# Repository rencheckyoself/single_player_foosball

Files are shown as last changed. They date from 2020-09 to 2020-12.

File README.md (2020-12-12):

# Single Player Foosball Table

[Video](https://mrencheck.wixsite.com/michaelrencheck/single-player-foosball)

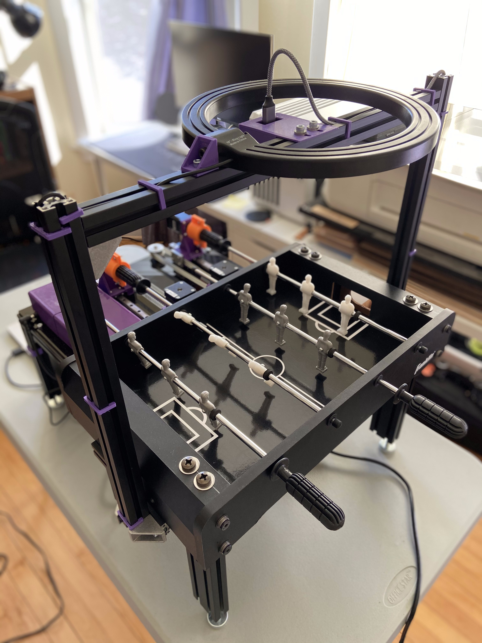
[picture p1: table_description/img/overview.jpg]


## Dependencies
The following are other software packages required to run the software for the table:
  - ROS Melodic
  - Pololu tic Software
  - OpenCV

## Installation

Begin by installing some of the external software dependancies:
  - The instructions for installing ROS Melodic are found [here](http://wiki.ros.org/melodic/Installation/Ubuntu).

  - The instructions to install the Pololu tic Software are found [here](https://github.com/pololu/pololu-tic-software). See relevant section in the BUILDING.md file to build the library from source, these were the [directions](https://github.com/pololu/pololu-tic-software/blob/master/BUILDING.md#building-from-source-on-linux-for-linux) I used.

After installing these create a new catkin workspace and clone this repository:

```
mkdir SinglePlayerFoosball
cd SinglePlayerFoosball
git clone https://github.com/rencheckyoself/single_player_foosball.git src
```

Then go into the repository and use wstool. This will download my forked version of the oCam package. It has been updated to function properly with ROS Melodic and adds some extra configuration for including the main launch file.
```
cd src
wstool update
```

Finally, go back to the top level of the directory and build the workspace:
```
cd ..
catkin_make
```

## Table Assembly

The CAD and Bill of Materials are located at this google drive [link](https://drive.google.com/drive/folders/1ccFXVZE29upyrK4uFZC98GBmM7wjYVV8?usp=sharing). You will an assembly procedure along with pictures depicting some of my build process and final assembly.

## Visualizations

This workspace includes two methods of visualizations, a urdf model displayed in rviz and an OpenCV window of the camera feed with added data.

#### rviz
 The urdf model will responds to all of the joint state messages displaying the positions that the gameplay node has decided to move to. It will also show a marker for most recent location of the ball.

#### OpenCV window
This window is generated by the `opencv_viewer` node. This will update everytime the camera sends a new image. The top corner shows the approximate frame rate of the images coming in. A red dot at the location of the most current ball position at the time an image is received. If the `ball_tracking` node does not detect a ball, the dot will appear in the upper left hand corner of the image. Also displayed is the player angle detection results. A white rectangle will show the ROI the `player_tracking` node is using and when the rods move, another rectangle will bound the detected player. A blue rectangle means the player is detected as down and the ball cannot pass underneath, green means the players are raised and at the end of a kick, red means the players are raises with their feet closest to the goal.

## Required Configuration
1. Update `table_motor_control/config/motor_ids.yaml` with the serial numbers for your specific TIC boards and update motor settings.

2. Calibrate your camera. I have included the calibration file for my camera in the ocam package files, but it may not be suitable for yours.
3. If you are using a different ball and/or table you may need to retrain the cascade classifier.
4. Update the pixel locations for the known pairs of world locations to pixel locations in order to calculate the homography.
5. Update the parameters to generate the joint_states/stepper commands to account for the differences in the camera position and calibration.
6. Update the parameters for the player angle detection.

### Tic Serial Numbers and Settings:
Once everything is wired and after installing the tic software, open a terminal and use the command `ticgui`. Plug in boards one at a time and copy over the serial number to the `motor_ids.yaml` file. Be sure that the serial numbers are copied over to the correct parameter in the yaml file.

Then you will want to determine the appropriate settings, namely the motor direction, max velocity, max acceleration, and current limit. The easiest way to do this is using the ticgui. Use [this](https://www.youtube.com/watch?v=-cAjdT6QN_w) quickstart video walkthrough for how to set the values. Then

### Camera Calibration:
There is a calibration file included in the ocam package from the .rosinstall file. This may or may not work for your ocam camera, so in order to generate your own calibration file, use the [`camera_calibration`](http://wiki.ros.org/camera_calibration) package in the ROS Image Pipeline. There is an included checkerboard in the `table_vision_sensing/calibration` directory to print out and use for the calibration.
Use the commands below to start the calibration using the included checkerboard:
```
roslaunch ocam ocam_ros.launch show_image:=false

rosrun camera_calibration cameracalibrator.py --size 7x5 --square 0.033 image:=/camera/image camera:=/camera
```
Once everything launches, move the checkerboard around in the image until the calibration button becomes available. Click calibrate and wait for the process to finish. The location of the output with be show in the terminal. Copy the `camera.yaml` generated by the calibration into `ocam/config`.

### Training the cascade classifier:
I have included the model I trained in the `cascade_data` folder, but if you don't have the same table/ball as my set up or want to experiment you can train your own cascade model.

OpenCV provides a great [walk-through](https://docs.opencv.org/3.4/dc/d88/tutorial_traincascade.html) for how to use their provided tools to generate the final output. Read through this first, then use the following to help with collecting your image dataset and generating the trained model.

To collect your own image set using the camera mounted over the table use the `capture_training_image.launch` file. This file will start nodes that create a new directory inside the `table_vision_sensing` package called `training_data`. Inside will be the `.dat` files required for the OpenCV training pipeline and two directories corresponding to the saved images. After launching, two windows will be displayed one called "Capture for background" and "Capture for ball".
 - To save an image for the background/negative set, click on the "Capture for background" window and click the "s" key. The picture will be saved in `training_data/background` directory and the proper annotation recorded in the `background.dat` file. All of the images in the background set should not contain the ball.
 - To save an image for the ball/positive set, click on the "Capture for ball" window and click the "s" key. The picture will be saved in the `training_data/ball` directory. Use the opencv tool for annotating positive images after all have been collected.

If you want to add you your collected set later, just relaunch the file and the numbering for the ball and background images will pick up where each set left off. Modify the `image_group` launch file argument to save positive images to a new directory.

```
roslaunch table_vision_sensing capture_training_data.launch image_group:=ball
```

You can also use the camera to capture gameplay footage and then use vlc to extract frames from the video and save them as images. I used the camera launch file then used a screen recorder to capture the OpenCV window.

```
roslaunch table_vision_sensing start_ocam.launch view_image:=true show_ball_pos:=false show_player_angle:=false
```

Once the video is captured, either follow [this](https://www.raymond.cc/blog/extract-video-frames-to-images-using-vlc-media-player/) to use the vlc gui to save out frames as images or use the following command:
```
cd [path_to_workspace]/src/table_vision_sensing
mkdir training_data/gameplay_frames
cvlc [video_name] --video-filter=scene --vout dummy --scene-ratio 60 --scene-path src/table_vision_sensing/training_data/ball/ --scene-prefix gameplay --start-time 0 --stop-time 120 vlc://quit
```
- --scene-prefix: a unique name to append to the beginning of each saved frame. (optional)
- --start-time: time to start at in seconds (optional)
- --stop-time: time to stop at in seconds (optional)
- --scene-ratio: how often to save frames. i.e. a scene-ratio of 60 for a video recorded at 60 fps will save 1 image every second.

Each time you run the command the number will always start at 1 regardless of the time span used so if your want to use a bunch of small pieces of the video, modify the --scene-prefix to avoid overwriting previously generated images. Also if you use the command line, I got a lot of error messages that popped up, but it didn't effect the functionality. The command will terminate once all of the frames have been saved. See the [VLC Documentation](https://wiki.videolan.org/VLC_command-line_help) for more information or use `vlc --full-help`.

Data collection tips:
- Collect all of the pictures with the overhead light on.
- If your ball has a pattern, be sure to rotate the ball between still image shots.
- Take picture of the ball partially occluded by the players and rods.
- Take background pictures with the players in various orientations.
- Take pictures of the ball when it is moving fast as well as slow.

You will want to collect 2:1 positive to background images. I used roughly 1000 positive images and 500 background images. After all of your images are collected, use the integrated annotation tool provided by OpenCV to properly annotate the ball/positive image set. It should take about 45min to annotate 1000 positive images. Using the following:
```
cd [path_to_workspace]/src/table_vision_sensing/training_data
opencv_annotation --annotations  -ball.dat --images ball/
```

After the annotations have been completed, use the provided OpenCV tool to create the positive image set .vec file. Use the following command:
```
cd [path_to_workspace]/src/table_vision_sensing/training_data
opencv_createsamples -vec ball.vec -info ball.dat -w 24 -h 24 -num [number of images]
```

After the .vec file has been generated, use the cascade trainer to get the trained cascade model for ball detection. The following was my configuration but your mileage may vary. I also tweaked the minHitRate to 0.999 and maxFalseAlarmRate to 0.1 as well. See the OpenCV documentation for all of the possible training parameters to play with.
```
cd [path_to_workspace]/src/table_vision_sensing/training_data
mkdir ../cascade_data
opencv_traincascade -data ../cascade_data/ -vec ball.vec -bg background.dat -w 24 -h 24 -numPos 700 -numNeg 500 -numStages 25
```

### Homography Calculation
In order to transform the ball's image coordinates to world coordinates, the system needs to know some known pairs. So you will need to update the `homography_config.yaml` file in the `table_gameplay_ai/config` directory to adjust for the slight differences in the camera location. Included in that directory is a template corresponding to the world positions already listed in the `homography_config.yaml` file and an .stl for a stand that neatly fits into the circles on the template. Print out two copies of the template, attach them along the middle and and place it on the field.

Then start up the ball tracking node, echo the `/BallPosition` topic in a separate terminal and record the average `(x,y)` pixel values in the `.yaml` file. Be sure that as the image coordinates are entered in to the .yaml file, they are entered on the correct line.

```
roslaunch table_vision_sensing start_tracking.launch view_image:=true
rostopic echo /BallPosition
```

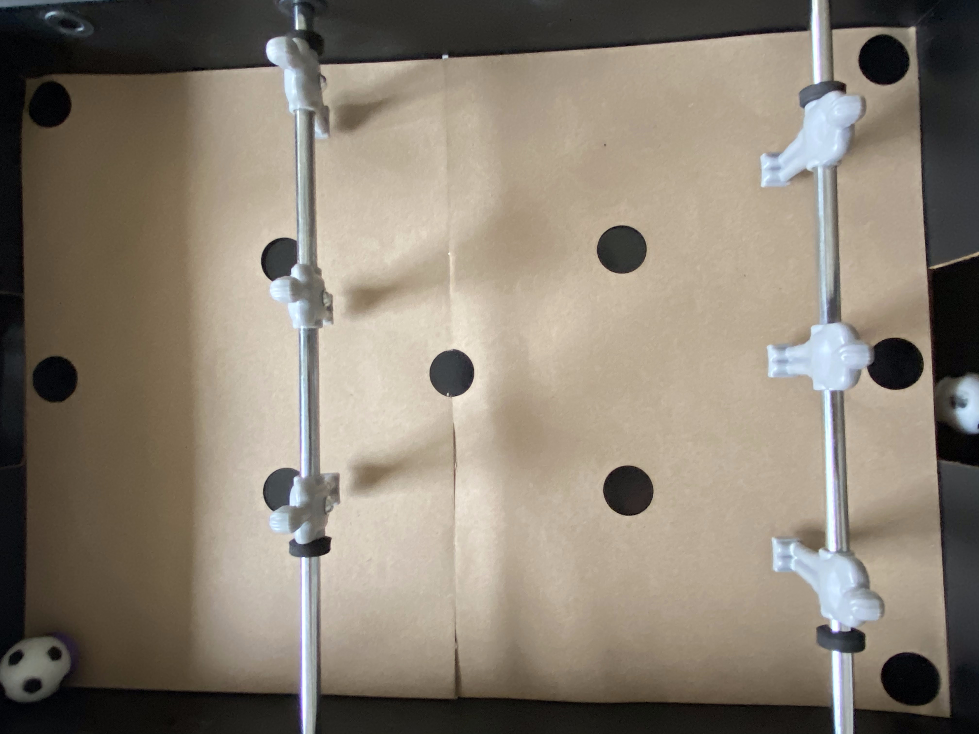
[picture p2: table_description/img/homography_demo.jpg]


### Command Generation Configuration

The two parameters that will most likely need adjusted are the `def_rod_xpos` and the `fwd_rod_xpos` in the `command_generation_config.yaml`. These parameters define the x position of the ideal location to strike the ball for each rod. In order to update these, use `start_game.launch` but leave the motors unpowered so the rods stay stationary. Position the players vertically and place the ball directly in front of a player. Either use rviz or echo the `visualization_marker` topic to see the x position of the ball in the world coordinates. Record this value in the `command_generation_config.yaml` file for the automated defensive rod and the automated offensive rod.

If you are using a different sized table, you will need to update the joint limits as well to account for linear travel of the rod. You may also want to update `table_params.yaml` in the `table_description` package in order to correct the visualization. For example, the rods on my table can travel 0.09m linearly. The urdf assumes the 0 position is in the middle so the joint limits will be at -0.45 and 0.45. For my table, 0.09m corresponds to roughly 240 steps to make the rod travel the full distance. When the game starts up, the gameplay node assumes the rod is already in 0 position. I chose to have the lower stepper position limit be the 0 position which makes the upper stepper position limit 240.

You can also modify the `linear_hysteresis` parameter to make the linear motion more or less sensitive to changes in the ball position.

### Player Angle Detection Configuration

You may need to adjust the player angle detection parameters in `player_angle_detection.yaml` to account for your camera's position and calibration. Use the `start_tracking.launch` file with `view_image:=true` to display results of the player angle detection. First modify the roi_x and roi_y, roi_width, and roi_height so that the large white rectangles capture one of the players on the two automated rods.

After the windows are properly aligned use rostopic echo to listen to the `\Def_RodState` and `\Fwd_RodState`. The player detection works using background subtraction, so in order use the detection the rod needs to move. Rotate the rod parallel to the table (like it just finished a kick) and slowly move it back and forth. Update `end_kick_x` value to a something a few less than the `min_x_value` shown on the topic and update `end_kick_width` to something a few less than the maximum `bounding_rect_img.width` value shown on the   topic.

If the bounding rectangle is not showing up when the player is moving, decrease `area_limit`. If small contours that are not part of the player are being detected, increase `area_limit`.

## How to Run:

Position players in the assumed starting position: the players feet down, perpendicular to the table with the rod against the wall closest to the motors, like so:

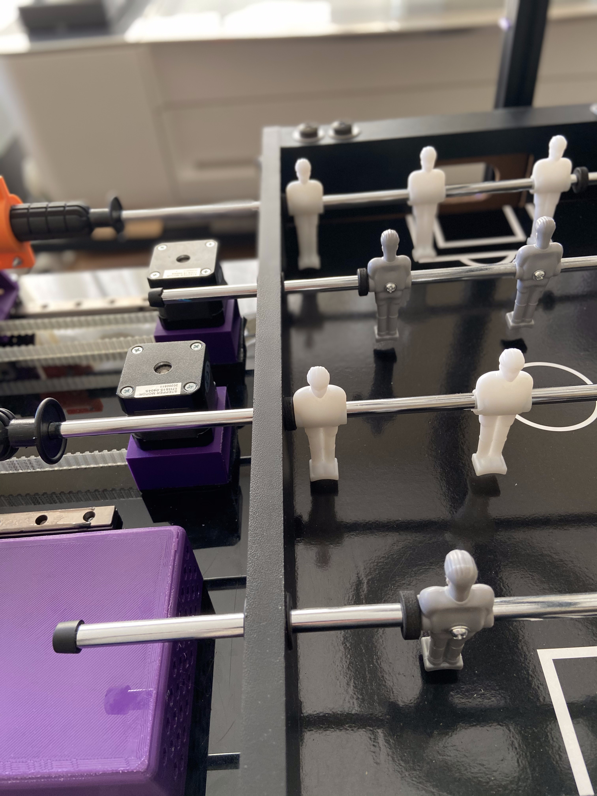
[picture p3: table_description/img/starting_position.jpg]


Plug in power supply to the barrel jack connector, then plug it into the wall and flip the switch to turn on the table.

Launch main launch file:
```
roslaunch table_gameplay_ai start_game.launch with_rviz:=false view_image:=false
```

Throw ball onto table and play!

Change the `mode` argument type to change the play style of the table:
- 0: (default) Open loop. Relies on the accuracy of the stepper controller position count to move.
- 1: Infinite spin. The linear position control stays the same as mode 0, but the rods will continually spin.
- 2: Rotation feedback. Same linear control scheme, but the angular control uses the player angle detection to account for any slipping during gameplay.

## Packages

### Description
This package provides a urdf model of the foosball table that can be displayed in rviz.

Launch Files:
- `view_table.launch`: Launch rviz and display the urdf along with the joint state publisher gui.
  - use_gui, default: true. Set this to false to turn off the joint state publisher
  - rviz_config, the location of the rviz configuration file
  - with_rviz, default: true. Set to false to not launch rviz.

Configuration:
- `table_params.yaml`: measurements of the physical table. Changing these will update the urdf.

### Control
This package provides an interface to work with the TIC Stepper Controller API through ROS by offering services.

Launch Files:
- `tic_controllers.launch`: launch all of the nodes to interact with the motors

Nodes:
- `tic_cmd`: node that starts up services to manually interact with each controller. If a controller is not connected, this will not launch properly.

Configuration:
- `motor_ids.yaml`: contains all of the identifying information for each controller. This file must be updated with the serial numbers for your purchased boards.
- `*_settings.txt`: these files contain the detailed settings for each of the motors. They were initially generated by exporting the settings using the ticgui. These files can be used to update the settings of a given tic while everything is running using the `*_update_settings` service. The can also be uploaded using the ticgui tool.

### Vision
This package is currently set up to follow the [ROS image_pipeline](http://wiki.ros.org/image_pipeline) structure. The `table_vision_sensing` package is set up to be camera agnostic, so feel free to use your own camera in place of the one linked in the parts list. You will need to modify the launch files to use your own camera.

Launch Files:
- `start_ocam.launch`: Launch the camera and view the rectified image
  - view_image, default: false. Set this to false to the rectified image.
  - show_ball_pos, default: true. Set this to false to not display a red dot for the ball position on the image feed.
  - show_player_angle, default: true. Set to false to not display bounding rectangles for the player angle.
- `start_tracking.launch`: Launch the ball and player tracking nodes. set view_image to true to view the output.
  - view_image, default: false. Set this to false to the rectified image.
- `capture_training_data.launch`: Launch everything to collect images to train the cascade classifier
  - image_group, default: "ball". A string to use as the name for a directory of positive images.

Nodes:
 - `ball_tracking`: Use the trained cascade model to find and publish the ball's pixel location
 - `opencv_viewer`: Listen to an image topic and display the image along with the ball position and player angle info
 - `player_tracking`: Use background subtraction and contour fitting to determine the approximate angle of the player
 - `training_image_capture`: Listen to an image topic to collect data to train a cascade classifier

Configuration:
 - `player_angle_detection.yaml`: contains all of parameters to define the window to analyze and the parameters to detect if the players are raised and which side the feet are closest to.

### Gamplay
This package is used as the main decision making pipeline based on the detected ball position and creates a joint state message that can be used by the urdf model for testing or converted to stepper commands using the `table_motor_control` package.

Launch Files:
- `start_game.launch`: Launches everything to play a game of foosball against the table
  - with_rviz, default: true. Set to false to not launch rviz.
  - view_image, default: false. Set this to false to the rectified image.
- `start_simulation.launch`: Uses the real ball position on the table, but does not actuate the real motors only the urdf model in rviz.

Nodes:
- `follow_ball`: The main node to decide the action and publish the joint state message.

Config:
- `homography_config.yaml`: contains know pairs of world location to pixel location in order to calculate the homography.

## Resources
- [Tic User Manual](https://www.pololu.com/docs/0J71)
- [OpenCV Documentation](https://www.docs.opencv.org/master/)
- [ROS Image Pipeline](http://wiki.ros.org/image_pipeline)
- [oCam Manual](http://withrobot.com/en/camera/ocam-1cgn-u-t/)

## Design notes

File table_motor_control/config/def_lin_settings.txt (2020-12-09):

# Pololu Tic USB Stepper Controller settings file.
# https://www.pololu.com/docs/0J71
product: T825
control_mode: serial
never_sleep: false
disable_safe_start: false
ignore_err_line_high: false
auto_clear_driver_error: true
soft_error_response: decel_to_hold
soft_error_position: 0
serial_baud_rate: 9600
serial_device_number: 14
serial_alt_device_number: 0
serial_enable_alt_device_number: false
serial_14bit_device_number: false
command_timeout: 0
serial_crc_for_commands: false
serial_crc_for_responses: false
serial_7bit_responses: false
serial_response_delay: 0
vin_calibration: 0
input_averaging_enabled: true
input_hysteresis: 0
input_scaling_degree: linear
input_invert: false
input_min: 0
input_neutral_min: 2015
input_neutral_max: 2080
input_max: 4095
output_min: 0
output_max: 240
encoder_prescaler: 1
encoder_postscaler: 1
encoder_unlimited: false
scl_config: default
sda_config: default
tx_config: default
rx_config: default
rc_config: default
invert_motor_direction: false
max_speed: 13000000
starting_speed: 0
max_accel: 1300000
max_decel: 0
step_mode: 1
current_limit: 384
current_limit_during_error: -1
decay_mode: slow
auto_homing: false
auto_homing_forward: false
homing_speed_towards: 1000000
homing_speed_away: 500000

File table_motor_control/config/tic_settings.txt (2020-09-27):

# Pololu Tic USB Stepper Controller settings file.
# https://www.pololu.com/docs/0J71
product: T825
control_mode: serial
never_sleep: false
disable_safe_start: false
ignore_err_line_high: false
auto_clear_driver_error: true
soft_error_response: decel_to_hold
soft_error_position: 0
serial_baud_rate: 9600
serial_device_number: 14
serial_alt_device_number: 0
serial_enable_alt_device_number: false
serial_14bit_device_number: false
command_timeout: 1000
serial_crc_for_commands: false
serial_crc_for_responses: false
serial_7bit_responses: false
serial_response_delay: 0
vin_calibration: 0
input_averaging_enabled: true
input_hysteresis: 0
input_scaling_degree: linear
input_invert: false
input_min: 0
input_neutral_min: 2015
input_neutral_max: 2080
input_max: 4095
output_min: -200
output_max: 200
encoder_prescaler: 1
encoder_postscaler: 1
encoder_unlimited: false
scl_config: default
sda_config: default
tx_config: default
rx_config: default
rc_config: default
invert_motor_direction: true
max_speed: 3000000
starting_speed: 0
max_accel: 40000
max_decel: 0
step_mode: 1
current_limit: 192
current_limit_during_error: -1
decay_mode: mixed
auto_homing: false
auto_homing_forward: false
homing_speed_towards: 1000000
homing_speed_away: 500000

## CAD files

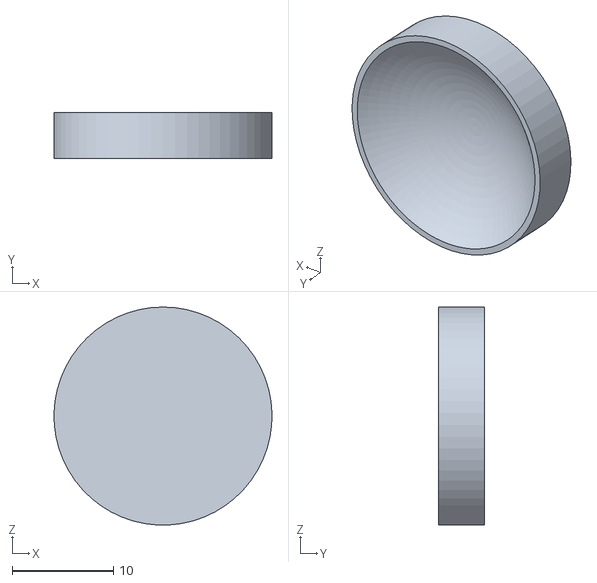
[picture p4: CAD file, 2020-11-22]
table_gameplay_ai/config/BallStandShort.STL
21.5 x 4.50 x 21.5

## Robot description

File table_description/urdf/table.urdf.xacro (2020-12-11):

<?xml version="1.0"?>
<robot xmlns:xacro="http://www.ros.org/wiki/xacro" name="table">

  <xacro:property name="props" value="${load_yaml('$(find table_description)/config/table_params.yaml')}"/>

  <xacro:property name="rod_length" value="${props['rod_length']}"/>
  <xacro:property name="rod_diameter" value="${props['rod_diameter']}"/>
  <xacro:property name="rod_mountingheight" value="${props['rod_mountingheight']}"/>

  <xacro:property name="player_width" value="${props['player_width']}"/>
  <xacro:property name="player_depth" value="${props['player_depth']}"/>
  <xacro:property name="player_height" value="${props['player_height']}"/>
  <xacro:property name="player_mountingheight" value="${props['rod_mountingheight']}"/>

  <xacro:property name="ball_diameter" value="${props['ball_diameter']}"/>

  <xacro:property name="field_width" value="${props['field_width']}"/>
  <xacro:property name="field_length" value="${props['field_length']}"/>
  <xacro:property name="field_thickness" value="0.005"/>

  <xacro:property name="goal_width" value="${props['goal_width']}"/>
  <xacro:property name="goal_height" value="${props['goal_height']}"/>

  <xacro:property name="wall_height" value="${props['wall_height']}"/>

  <xacro:property name="attack_rod_distance" value="${props['attack_rod_distance']}"/>
  <xacro:property name="goalie_rod_distance" value="${props['goalie_rod_distance']}"/>

  <xacro:property name="rod_travel_distance" value="${props['rod_travel_distance']}"/>

  <xacro:property name="wall_thickness" value="0.015"/>

  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
  <xacro:macro name="player" params="rod_name player_num r g b">
    <link name="${rod_name}_player_${player_num}">
      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
    </link>

    <joint name="${rod_name}_player_${player_num}_joint" type="fixed">
      <parent link="${name}_p${player_num}_mount"/>
      <child link="${rod_name}_player_${player_num}"/>
    </joint>

  </xacro:macro>

  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
  <xacro:macro name="player_rod" params="name dir dist r g b">
    <link name="${name}_mount_c">
      <origin xyz="0 0 0" rpy="0 0 0"/>
    </link>

    <link name="${name}_mount_p">
      <origin xyz="0 0 0" rpy="0 0 0"/>
    </link>

    <link name="${name}_rod">
      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
    </link>

    <joint name="${name}_fixed_joint" type="fixed">
      <origin xyz="${dir*dist} ${-field_width/2} ${rod_mountingheight}"/>
      <parent link="table_base"/>
      <child link="${name}_mount_c"/>
    </joint>

    <joint name="${name}_rot_joint" type="continuous">
      <parent link="${name}_mount_c"/>
      <child link="${name}_mount_p"/>
      <axis xyz="0 1 0"/>
    </joint>

    <joint name="${name}_lin_joint" type="prismatic">
      <origin xyz="0 0 0" rpy="0 0 0"/>
      <parent link="${name}_mount_p"/>
      <child link="${name}_rod"/>
      <axis xyz="0 1 0"/>
      <limit upper="${rod_travel_distance/2}" lower="${-rod_travel_distance/2}" effort="10" velocity="2"/>
    </joint>

    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
    <link name="${name}_p1_mount"/>
    <link name="${name}_p2_mount"/>
    <link name="${name}_p3_mount"/>

    <joint name="${name}_p1_mount_joint" type="fixed">
      <origin xyz="0 0.061 0" rpy="0 0 0"/>
      <parent link="${name}_rod"/>
      <child link="${name}_p1_mount"/>
    </joint>

    <joint name="${name}_p2_mount_joint" type="fixed">
      <origin xyz="0 0.141 0" rpy="0 0 0"/>
      <parent link="${name}_rod"/>
      <child link="${name}_p2_mount"/>
    </joint>

    <joint name="${name}_p3_mount_joint" type="fixed">
      <origin xyz="0 0.221 0" rpy="0 0 0"/>
      <parent link="${name}_rod"/>
      <child link="${name}_p3_mount"/>
    </joint>

    <xacro:player rod_name="${name}" player_num="1" r="${r}" g="${g}" b="${b}"/>
    <xacro:player rod_name="${name}" player_num="2" r="${r}" g="${g}" b="${b}"/>
    <xacro:player rod_name="${name}" player_num="3" r="${r}" g="${g}" b="${b}"/>

  </xacro:macro>

  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
  <xacro:macro name="side_wall" params="side dir">
    <link name="${side}_side_wall">
      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
    </link>

    <joint name="${side}_side_wall_joint" type="fixed">
      <origin xyz="0 ${dir*field_width/2} 0" rpy="0 0 0" />
      <parent link="table_base"/>
      <child link="${side}_side_wall"/>
    </joint>
  </xacro:macro>

  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
  <xacro:macro name="end_wall" params="side dir">
    <link name="${side}_end_wall_goal">
      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
    </link>

    <joint name="${side}_end_wall_joint" type="fixed">
      <origin xyz="${dir*field_length/2} 0 ${0}" rpy="0 0 0" />
      <parent link="table_base"/>
      <child link="${side}_end_wall_goal"/>
    </joint>

    <xacro:end_wall_segment end_color="${side}" end_dir="${dir}" side="right" dir="1"/>
    <xacro:end_wall_segment end_color="${side}" end_dir="${dir}" side="left" dir="-1"/>

  </xacro:macro>
  <xacro:macro name="end_wall_segment" params="end_color end_dir side dir">
    <link name="${end_color}_end_wall_${side}">
      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
    </link>

    <joint name="${end_color}_end_wall_${side}_joint" type="fixed">
      <origin xyz="0 ${dir*(goal_width/2 + (field_width-goal_width)/4)} 0" rpy="0 0 0" />
      <parent link="${end_color}_end_wall_goal"/>
      <child link="${end_color}_end_wall_${side}"/>
    </joint>
  </xacro:macro>

  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
  <link name="base_link">
    <origin xyz="0 0 0" rpy="0 0 0"/>
  </link>

  <link name="table_base">
    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
  </link>
  <joint name="table_base_joint" type="fixed">
    <origin xyz="0 0 0" rpy="0 0 0" />
    <parent link="base_link"/>
    <child link="table_base"/>
  </joint>

  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
  <link name="field">
    <origin xyz="0 0 0" rpy="0 0 0"/>
  </link>
  <joint name="field_joint" type="fixed">
    <origin xyz="${(-field_length + ball_diameter)/2} ${(-field_width + ball_diameter)/2} 0" rpy="0 0 0" />
    <parent link="base_link"/>
    <child link="field"/>
  </joint>

  <xacro:side_wall side="right" dir="1"/>
  <xacro:side_wall side="left" dir="-1"/>

  <xacro:end_wall side="white" dir="1"/>
  <xacro:end_wall side="grey" dir="-1"/>

  <xacro:player_rod name="white_attack" dir="1" dist="${attack_rod_distance}" r="1" g="1" b="1"/>
  <xacro:player_rod name="white_goalie" dir="-1" dist="${goalie_rod_distance}" r="1" g="1" b="1"/>

  <xacro:player_rod name="grey_attack" dir="-1" dist="${attack_rod_distance}" r="0.5" g="0.5" b="0.5"/>
  <xacro:player_rod name="grey_goalie" dir="1" dist="${goalie_rod_distance}" r="0.5" g="0.5" b="0.5"/>

</robot>

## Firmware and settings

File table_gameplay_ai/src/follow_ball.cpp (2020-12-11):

/// \file
/// \brief Node to subsribe to commands and send them to the Tic's. Also offers services for manual control.
/// PARAMETERS:
///   table_gameplay_ai/config/homography_config.yaml
///   table_gameplay_ai/config/command_generation_config.yaml
///   table_motor_control/config/motor_ids.yaml
/// PUBLISHES:
///   /joint_states (sensor_msgs/JointState) A joint state message for visualization in rviz
///   /visualization_marker (visualization_msgs/Marker) A marker to show the balls position in world coordinates
/// SUBSCRIBES:
///   /BallPosition (geometry_msgs/Point) The image coordinates of the ball
///   /Def_RodState (table_vision_sensing/RosState) Rod state information for the defensive rod
///   /Fwd_RodState (table_vision_sensing/RosState) Rod state information for the offensive rod
/// SERIVCES:
///   /*_update_settings (std_msgs/Empty) services to update the settings of the Tic Controllers.

#include <utility>
#include <memory>

#include <ros/ros.h>

#include <XmlRpcValue.h>

#include <sensor_msgs/JointState.h>
#include <visualization_msgs/Marker.h>

#include "table_vision_sensing/RodState.h"

#include "ball_prediction.hpp"
#include "table_ai.hpp"

static tracking::RodState fwd_rod_state, def_rod_state; ///< store the most recent rod state information

/// \brief Callback for the forward rod state suscriber
/// \param msg rod state information
void forwardRodCB(table_vision_sensing::RodState msg)
{
  fwd_rod_state.rod_is_up = msg.rod_is_up;
  fwd_rod_state.players_are_back = msg.players_are_back;
}

/// \brief Callback for the forward rod state suscriber
/// \param msg rod state information
void defenseRodCB(table_vision_sensing::RodState msg)
{
  def_rod_state.rod_is_up = msg.rod_is_up;
  def_rod_state.players_are_back = msg.players_are_back;
}

/// \brief main function to create the real_waypoints node
/// \param argc argument count
/// \param arguments
/// \returns success
int main(int argc, char** argv)
{
  ros::init(argc, argv, "follow_ball");

  ros::NodeHandle np("~");
  ros::NodeHandle n;

  ros::Publisher joint_pub = n.advertise<sensor_msgs::JointState>("joint_states", 1);
  ros::Publisher vis_pub = n.advertise<visualization_msgs::Marker>( "visualization_marker", 1);

  ros::Subscriber def_rod_sub = n.subscribe<table_vision_sensing::RodState>("/Def_RodState", 1, defenseRodCB);
  ros::Subscriber fwd_rod_sub = n.subscribe<table_vision_sensing::RodState>("/Fwd_RodState", 1, forwardRodCB);

  XmlRpc::XmlRpcValue world_coordinates;
  XmlRpc::XmlRpcValue image_coordinates;
  double error_threshold;

  table::ControllerInfo tic_info;
  table::CalibrationVals config;

  int mode;

  // Read in mode
  np.getParam("mode", mode);

  // Read in homography configuration
  np.getParam("world_coordinates", world_coordinates);
  np.getParam("image_coordinates", image_coordinates);
  np.getParam("error_threshold", error_threshold);

  // Read in tic controller configurations
  np.getParam("fwd_rot/serial_number", tic_info.fwd_rot_sn);
  np.getParam("fwd_rot/nickname", tic_info.fwd_rot_nickname);

  np.getParam("fwd_lin/serial_number", tic_info.fwd_lin_sn);
  np.getParam("fwd_lin/nickname", tic_info.fwd_lin_nickname);

  np.getParam("def_rot/serial_number", tic_info.def_rot_sn);
  np.getParam("def_rot/nickname", tic_info.def_rot_nickname);

  np.getParam("def_lin/serial_number", tic_info.def_lin_sn);
  np.getParam("def_lin/nickname", tic_info.def_lin_nickname);

  // Read in configuration parameters
  np.getParam("lower_joint_limit", config.lin_joint_limits.first);
  np.getParam("upper_joint_limit", config.lin_joint_limits.second);

  np.getParam("lower_lin_steps", config.lin_step_limits.first);
  np.getParam("upper_lin_steps", config.lin_step_limits.second);

  np.getParam("linear_hysteresis", config.linear_hysteresis);

  np.getParam("kick_trigger_threshold", config.kick_trigger_threshold);

  np.getParam("def_rod_xpos", config.def_rod_xpos);
  np.getParam("fwd_rod_xpos", config.fwd_rod_xpos);

  np.getParam("velocity_modifier", config.velocity_modifier);

  np.getParam("def_reset_offset", config.def_reset_offset);
  np.getParam("fwd_reset_offset", config.fwd_reset_offset);
  np.getParam("full_rotation_offset", config.full_rotation_offset);

  ROS_INFO_STREAM("TICCMD: Forward Rotation Name: " << tic_info.fwd_rot_nickname);
  ROS_INFO_STREAM("TICCMD: Forward Rotation ID: " << tic_info.fwd_rot_sn);

  ROS_INFO_STREAM("TICCMD: Forward Linear Name: " << tic_info.fwd_lin_nickname);
  ROS_INFO_STREAM("TICCMD: Forward Linear ID: " << tic_info.fwd_lin_sn);

  ROS_INFO_STREAM("TICCMD: Defense Rotation Name: " << tic_info.def_rot_nickname);
  ROS_INFO_STREAM("TICCMD: Defense Rotation ID: " << tic_info.def_rot_sn);

  ROS_INFO_STREAM("TICCMD: Defense Linear Name: " << tic_info.def_lin_nickname);
  ROS_INFO_STREAM("TICCMD: Defense Linear ID: " << tic_info.def_lin_sn);

  // convert coordinate data to different data type
  std::vector<std::vector<double>> wc = tracking::parse_points_data(world_coordinates);
  std::vector<std::vector<double>> ic = tracking::parse_points_data(image_coordinates);

  // initialize ball tracking
  tracking::BallTracker foosball(0, wc, ic, error_threshold);
  foosball.testExtrinsicResults();

  config.xrange = foosball.getXRange();
  config.yrange = foosball.getYRange();

  // Create gameplay class based on the mode selected
  std::unique_ptr<table::RealFoosballTable> robot_player;

  switch(mode)
  {
    case 0:
    {
      robot_player = std::unique_ptr<table::RealFoosballTable>(new table::RealFoosballTable(tic_info, config));
      break;
    }
    case 1:
    {
      robot_player = std::unique_ptr<table::RealFoosballTable>(new table::DeathSpinTable(tic_info, config));
      break;
    }
    case 2:
    {
      robot_player = std::unique_ptr<table::RealFoosballTable>(new table::FeedbackTable(tic_info, config));
      break;
    }
    default:
    {
      ROS_ERROR_STREAM("Invalid Mode. Must use 0 (open loop mode), 1 (spin mode), or 2 (rotational feedback mode).");
      ros::shutdown();
    }
  }

  // initialize joint state message
  sensor_msgs::JointState joint_msg;
  std::vector<std::string> joint_names = {"white_attack_rot_joint", "white_attack_lin_joint", "white_goalie_rot_joint", "white_goalie_lin_joint", "grey_attack_rot_joint", "grey_attack_lin_joint", "grey_goalie_rot_joint", "grey_goalie_lin_joint"};
  joint_msg.name = joint_names;

  // initialize ball marker messageS
  visualization_msgs::Marker ball_marker;
  ball_marker.header.frame_id = "field";

  ros::Rate r(100);

  while(ros::ok())
  {
    // Get the position of the ball
    cv::Point3d pos = foosball.getWorldPosition();

    // generate the control and issue the commands
    robot_player->moveTable(pos, fwd_rod_state, def_rod_state);

    // build the joint state message
    std::vector<double> joint_vals = robot_player->getCurrentJointStates();

    joint_msg.header.stamp = ros::Time::now();
    joint_msg.position = joint_vals;

    joint_pub.publish(joint_msg);

    // build the marker message
    ball_marker.header.stamp = ros::Time::now();
    ball_marker.id = 0;
    ball_marker.type = visualization_msgs::Marker::SPHERE;
    ball_marker.action = visualization_msgs::Marker::ADD;
    ball_marker.pose.position.x = pos.x;
    ball_marker.pose.position.y = pos.y;
    ball_marker.pose.position.z = 0.01375;
    ball_marker.pose.orientation.x = 0.0;
    ball_marker.pose.orientation.y = 0.0;
    ball_marker.pose.orientation.z = 0.0;
    ball_marker.pose.orientation.w = 1.0;

    ball_marker.scale.x = 0.0275;
    ball_marker.scale.y = 0.0275;
    ball_marker.scale.z = 0.0275;

    ball_marker.color.a = 1.0;
    ball_marker.color.r = 0.1;
    ball_marker.color.g = 0.1;
    ball_marker.color.b = 0.1;

    vis_pub.publish(ball_marker);

    ros::spinOnce();

    r.sleep();
  }

  return 0;
}

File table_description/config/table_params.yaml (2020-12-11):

# all dimensions are in meters

# Visual Parameters
rod_length: 0.410 # length of the rod
rod_diameter: 0.0077 # diameter of the rod

rod_mountingheight: 0.049 # mounting height of the rods from the surface of the field

attack_rod_distance: 0.050 # distance from the centerline of the field to the attack rod
goalie_rod_distance: 0.145 # distance from the centerline of the field to the goalie rod

player_width: 0.014 # width of the kicking surface of the player
player_depth: 0.011 # thickess of the kicking surface of the player
player_height: 0.070 # height of the entire player
player_moutningheight: 0.042 # height of the mounting axis of the player to the rod from the bottom of the player

ball_diameter: 0.0274 # ball diameter

field_length: 0.402 # field length from goal to goal
field_width: 0.280 # field width from side to side

wall_height: 0.062 # height of the side walls

goal_height: 0.040 # height of the goal opening
goal_width: 0.080 # width of the goal opening

rod_travel_distance: 0.090 # the linear distance a rod can travel

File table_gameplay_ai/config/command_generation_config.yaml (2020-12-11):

upper_joint_limit: 0.045 # the upper linear joint limit in meters. This should match the urdf linear joint limit
lower_joint_limit: -0.045 # The lower linear joint limit in meters. This should match the urdf linear joint limit

upper_lin_steps: 230 # the upper linear joint limit for the actual stepper command
lower_lin_steps: 0 # the lower linear joint limit for the actual stepper command

linear_hysteresis: 10 # the smaller the value the more sensative the linear position command generation will be

kick_trigger_threshold: 0.015 # in meters, defines the +/- threshold to trigger a kick

def_rod_xpos: 0.067 # the x value (in world coordinates) of the ideal position for the defensive rod to strike the ball
fwd_rod_xpos: 0.257 # the x value (in world coordinates) of the ideal position for the offensive rod to strike the ball

velocity_modifier: 0.55 # a value from 0 < x <= 1, scales the maximum velocity setting without changing the value in the controller settings.

def_reset_offset: 70 # number of steps to rotate backward to reset after a kick. This is only used for the feedback mode.
fwd_reset_offset: 50 # number of steps to rotate backward to reset after a kick. This is only used for the feedback mode.
full_rotation_offset: 200 # number of steps to complete a full rotation. This is only used for the feedback mode.

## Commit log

2020-09-27 Initial Commit. Started working on the tic controller node
    [motor_ids.yaml]
2020-09-28 Added first service to update the settings.
    [motor_ids.yaml]
2020-09-29 Added rosinstall file for oCam package, settings files, and added more services to table_motor_control
    [motor_ids.yaml]
2020-10-10 started building the urdf for visualization
    [table.urdf.xacro]
2020-10-11 continue building urdf
    [table.urdf.xacro]
2020-10-11 Finished table urdf, ball will be represented with tf broadcaster
    [ball.xacro.urdf, table.urdf.xacro]
2020-10-22 updated readme and some documentation
    [motor_ids.yaml]
2020-10-24 Removed separated visualization to a separate node. Updated cascade model. Started gameplay package
    [motor_ids.yaml]
2020-11-09 hacked together accurate ball position estimation, integrating with the motors
    [ball.xacro.urdf, motor_ids.yaml, table.urdf.xacro]
2020-11-10 Functioning linear position command, need account for error cases and incorperate hysteresis
    [table.urdf.xacro]
2020-11-15 updated ball locations, need to adjust solve pnp
    [motor_ids.yaml]
2020-11-17 Fixed issue with position commands
    [follow_ball.cpp, tic_server.cpp]
2020-11-18 Table working! need to clean up code base
    [table.urdf.xacro]
2020-11-22 Updated Documentation
    [BallStandShort.STL]
2020-12-01 Finished Angle Detection, need to implement velocity control for the steppers and clean up vision package
2020-12-03 Updated kicking funtionality to reset if a kick has been completed. Still need to integrate angle feedback
    [command_generation_config.yaml, table_ai.cpp]
2020-12-06 Added velocity commands functionality, fixed static file paths to use ros::package::getPath
    [tic_server.cpp]
2020-12-11 Functional gameplay using angular feedback. Fixed bug in the viewer.
    [command_generation_config.yaml, follow_ball.cpp, player_angle_detection.yaml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]
2020-12-11 Updated comments
    [motor_ids.yaml, table.urdf.xacro]
